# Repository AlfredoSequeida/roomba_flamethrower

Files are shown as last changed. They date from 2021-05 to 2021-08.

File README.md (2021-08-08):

# Roomba Flamethrower
[Watch the video here](https://youtu.be/nNa-5zJv5F0)

demo

This repo contains all of the code, schematics, and 3d models for the Roomba Flamethrower project.

## Setup
This project uses a Raspberry pi Zero W running [Raspberry Pi OS Lite](https://www.raspberrypi.org/software/operating-systems/) as the "brains" of the build. Python 3.5 or newer is required to run the software.

- To use hardware-timed servo pulses and thus avoid jittering from multiple servos being controlled by the pi, this project uses the pigpio library. 
- The Xbox one controller is handled using evdev.
- Serial communication between the Roomba and the raspberry pi is handled using pyserial.

To facilitate the setup process, this repo includes a setup script. To run it, simply run the following command from the project's root directory

```
sudo sh setup.sh
```

In addition, if you want to set up the program to run on boot for a better user experience. You can use `crontab` to set up a cronjob for the intended user. As an example for the default `pi` user.

```
crontab -u pi -e
```

Then run the script on boot by adding the following line to the file.

```
@reboot python3 /full/path/to/project/dir/roomba_flamethrower/roomba_flamethrower/main.py
```

Then save the file. A quick note of caution, the Roomba class initiates a serial connection with the Roomba using `safe` mode by default. However, if you decide to change the mode to something else, you need to add the logic to properly return the Roomba to `safe` mode to avoid battery drain.

As part of the setup, you also need to pair the Xbox One Controller and the raspberry pi.

Disable Enhanced Re-Transmission Mode (not supported by the Xbox One Controller)
```
echo 'options bluetooth disable_ertm=Y' | sudo tee -a /etc/modprobe.d/bluetooth.conf
```

start bluetoothctl 
```
sudo bluetoothctl
```

Start pairing mode on the Xbox One controller and scan for the controller
```
agent on
default-agent
scan on
```

once you see the controller appear, connect to it using its address
```
connect XX:XX:XX:XX:XX:XX
```

trust the controller using its address for automatic connections on boot
```
trust XX:XX:XX:XX:XX:XX
```

### Controlls
By default, these are the control mappings for the Xbox One controller.

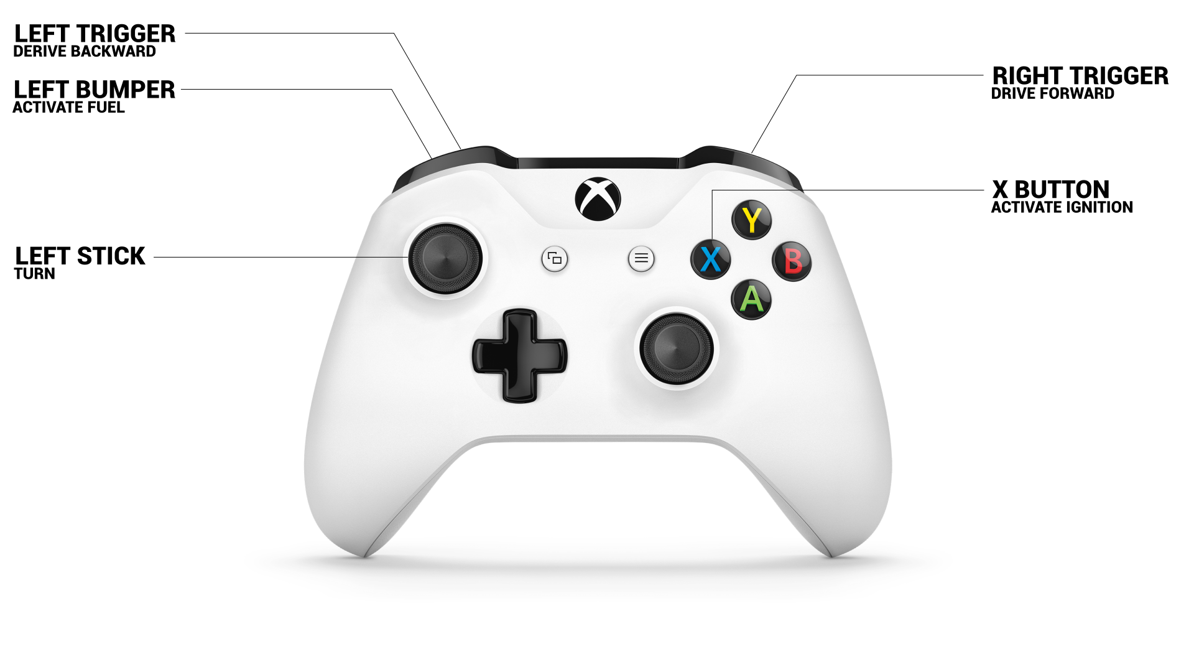
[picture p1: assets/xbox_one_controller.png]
controll mappings


If you want to change them, you can change the conditional statements in `main.py` in the `main()` function, which are found inside the for loop.

## Build
To build this project, the following parts were used:
- [(1) Raspberry Pi Zero W](https://www.raspberrypi.org/products/raspberry-pi-zero-w/)
- [(1) Micro USB Male to USB Female OTG Adapter](https://www.amazon.com/Ksmile®-Female-Adapter-SamSung-tablets/dp/B01C6032G0)
- (1) Xbox One Bluetooth Controller (1708)
- (1) Irobot Roomba 770
- [(1) Irbot Communication Cable for Create® 2](https://store.irobot.com/default/parts-and-accessories/create-accessories/communication-cable-for-create-2/4466502.html)
- [(2) 35kg-cm servos](https://www.amazon.com/ZOSKAY-Coreless-Digital-Stainless-arduino/dp/B07S9XZYN2)
- [(1) 12kg-cm servo](https://www.amazon.com/4-Pack-MG996R-Torque-Digital-Helicopter/dp/B07MFK266B)
- [(1) M2.5 brass stanoff kit](https://www.amazon.com/LBY-Multi-function-Combination-Screwdriver-Green/dp/B07GK6812D)
- [Neon 7X Refined Butane Gas Pack](https://www.amazon.com/Neon-Refined-Butane-300ml-Pack/dp/B072FR3LT2)
- [(1) Arc Lighter](https://www.amazon.com/lcfun-Waterproof-Windproof-Rechargeable-Flameless-Plasma-Camouflage/dp/B07GCHLDWR)
- [(1) USB Solar Power Bank](https://www.amazon.com/gp/product/B07T2NRK8G)
- [(1) USB A Male to Micro USB cable](https://www.amazon.com/10ft3Pack-Charging-Smartphone-Connection-Blackwhite/dp/B06XYH75NQ)

If you don't have it already, you may also need wire, solder, and a soldering iron.

In addition, to use the included 3d models, you will also need a 3d printer. I used the [Creality Ender 3 V2](https://www.amazon.com/Creality-Printer-Printing-Function-220x220x250mm/dp/B07FFTHMMN) and [White eSUN PLA+](https://www.amazon.com/eSUN-1-75mm-Printer-Filament-2-2lbs/dp/B01EKEMFQS) filament.

### 3D printing
All of the parts were printed using 10% infill with a 0.28mm layer height. The bed was set to 60° Celcius and the extruder to 225° Celcius. With the exception of the Raspberry Pi Zero base, all of the models were printed without using supports.

### Assembly
Besides the Roomba part of the build, the flame thrower part of the build is centered around the butane bottle.

The [bottle stand](https://github.com/AlfredoSequeida/roomba_flamethrower/blob/main/models/bottle_stand.stl) can be used to attach the butane bottle to the Roomba using an adhesive. An option like Hot Glue can allow you to easily remove it later by heating the glue back up.

Attached to the bottle stand you cand you can use string or rope along with the provided [hooks](https://github.com/AlfredoSequeida/roomba_flamethrower/blob/main/models/hook.stl) to latter hold down the bottle adapter when the butane servo uses a downward force to spray the bottle. 

The [bottle adapter](https://github.com/AlfredoSequeida/roomba_flamethrower/blob/main/models/bottle_adapter.stl) holds the two 35kg servos using the provided hardware, The butane servo uses the smaller plastic propeller with an M2.5 standoff through one of the holes, which aids in pressing down the [cap of the butane bottle](https://github.com/AlfredoSequeida/roomba_flamethrower/blob/main/models/cap.stl) and the lighter assembly servo uses the larger plastic propeller with two screws for holding down the servos attached to the [lighter assembly](https://github.com/AlfredoSequeida/roomba_flamethrower/blob/main/models/lighter_assembly.stl).

bottle adapter

Attached to the back portion of the bottle adapter is the [Raspberry Pi Zero base](https://github.com/AlfredoSequeida/roomba_flamethrower/blob/main/models/rpi_zero_base.stl). This base is set up with four M2.5 standoffs using screws on the underside. This is why the base has larger 4mm cylindrical cutouts on the underside. This provides a flush base that can be glued to the bottle adapter.

raspberry pi base

The lighter assembly holds the 12kg servo and the arc lighter. The servo is held in place and lifted using 3 brass standoffs. In addition, to press the button on the arc lighter, the metal adapter from the 35kg servos is attached. This is because this adapter has a much larger surface area compared to the included plastic adapters.

lighter assembly

## Wiring
To wire everything together, refer to the following schematic:

schematic

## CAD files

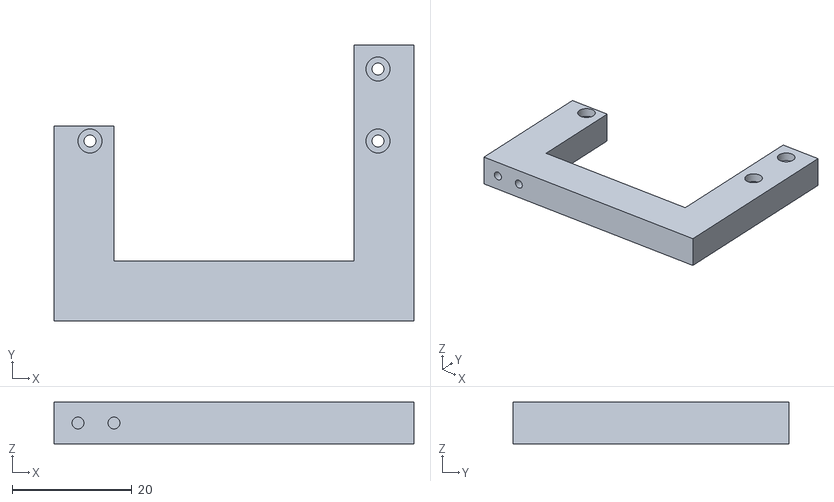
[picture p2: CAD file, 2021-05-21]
models/lighter_assembly.stl
60.0 x 46.0 x 7.00

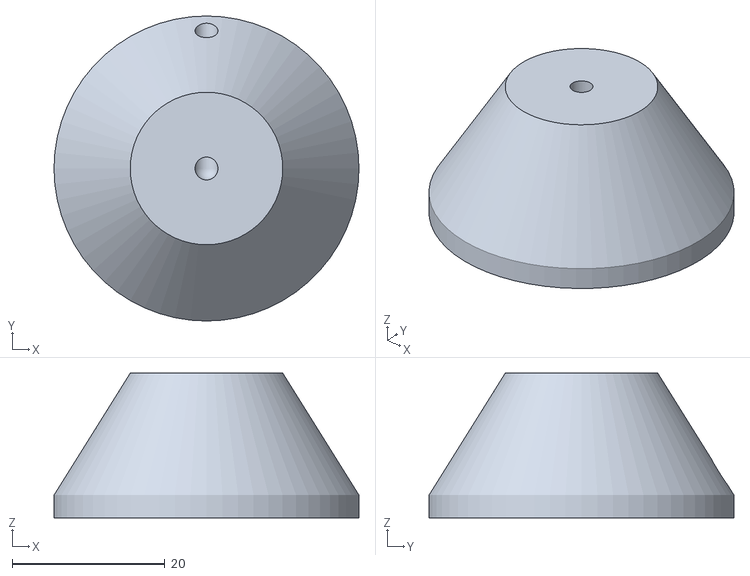
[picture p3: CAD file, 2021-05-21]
models/cap.stl
40.0 x 40.0 x 19.0

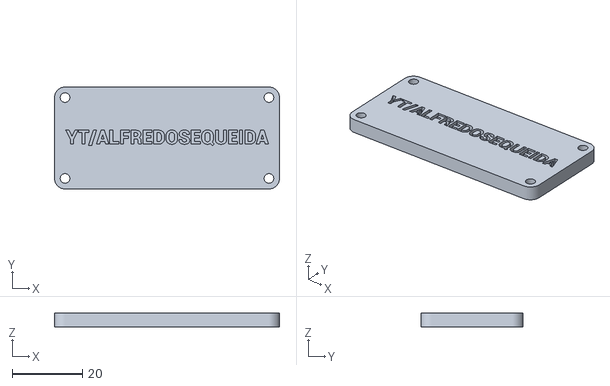
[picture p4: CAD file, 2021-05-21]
models/rpi_zero_base.stl
64.0 x 29.0 x 4.00

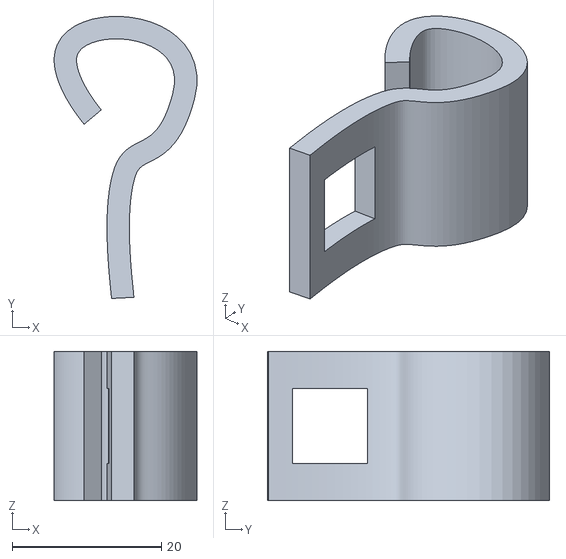
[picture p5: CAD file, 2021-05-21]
models/hook.stl
19.1 x 37.8 x 20.0

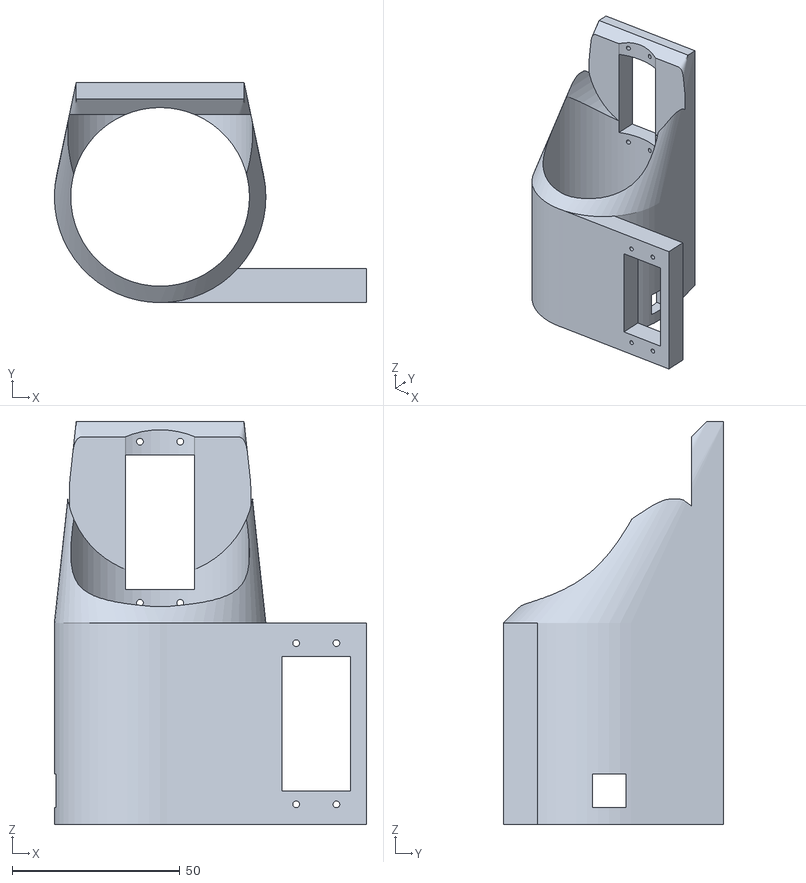
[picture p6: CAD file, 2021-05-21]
models/bottle_adapter.stl
93.0 x 65.6 x 120.0

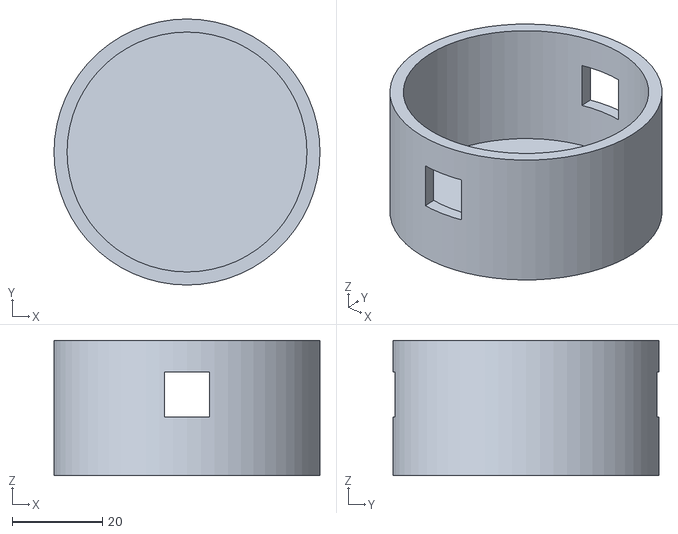
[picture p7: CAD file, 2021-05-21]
models/bottle_stand.stl
59.0 x 59.0 x 30.0

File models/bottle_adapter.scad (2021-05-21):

$fn=60;
bottle_r = 53/2;

holder_thickness = 5;

servo_y = 12;
servo_x = 20;
servo_z = 40;


// servo insert test
//difference(){
//    
//    bottle_adapter();
//
//    translate([15,-50,0])
//    cube([50,100,100]);
//
//    translate([-80,-50,0])
//    cube([100,50,100]);
//
//    translate([-65,-50,0])
//    cube([50,100,100]);
//}

bottle_adapter();

module bottle_adapter(){
    adapter_h = 120;
    insert_padding = 0.1;
    butane_channel_r = 10;
    butane_channel_h = 20;
    
    flat_surface_width = 50;
    
    servo_rotor_depth = 20;
    cap_depth = 8;
    
    servo_cutout_r = 56/2;
    
    hook_insert = 10;
    
    lighter_assembly_servo = [servo_x+40, servo_y-2, servo_z+20];

    difference(){
        union(){
        hull(){
            // butane servo
            translate([0,
                       bottle_r + holder_thickness + insert_padding,
                       adapter_h/2
                     ])
            rotate([0,0,90])
            cube([holder_thickness,
                  flat_surface_width,
                  adapter_h],
                center=true);

            cylinder(r=bottle_r + holder_thickness, h=adapter_h/2);
        }
            translate([bottle_r -25,
               -bottle_r/3 - servo_y *1.88,
               0
             ]){
        difference(){
            cube(lighter_assembly_servo);
    
            translate([(lighter_assembly_servo[0])/2 + 15,
                        lighter_assembly_servo[1]/1.3,
                        lighter_assembly_servo[2]/6])
            servo_insert();
        }
    }
    }
        
        cylinder(r=bottle_r + insert_padding, h=200);
        
        // servo insert
        translate([0,
                   bottle_r + holder_thickness,
                   adapter_h - servo_z - 10
                 ])
        servo_insert();
        
        translate([0,
                   bottle_r-2,
                   adapter_h - servo_cutout_r+10])
        rotate([90,0,0])
        cylinder(r=servo_cutout_r, h=20);
        
        translate([0,0,hook_insert])
        cube([100, hook_insert,hook_insert],center=true);
    }
}

module servo_insert(){
    offset = 7;
    
    screw_r = 2/2;
    normal_screw_r = 4/2;
    z_offset = 2;
    
    insert_padding = 0.5;
    insert_thickess = 20;
    
    holder_spacing_from_center = 4 + normal_screw_r;
    
    translate([0,0,servo_z/2])
    cube([insert_thickess + insert_padding,
          insert_thickess + insert_padding,
          servo_z],center=true);
    
    // top holes
    color("gold")
    translate([-holder_spacing_from_center,
               0,
               servo_z + z_offset + normal_screw_r
             ])
    rotate([90,0,0])
    cylinder(r=screw_r, h=insert_thickess, center=true);
    
    color("red")
    translate([-holder_spacing_from_center,
               insert_thickess/4,
               servo_z + z_offset + normal_screw_r
             ])
    rotate([90,0,0])
    cylinder(r=normal_screw_r, h=insert_thickess/2, center=true);
    
    color("gold")
    translate([holder_spacing_from_center,
               0,
               servo_z + z_offset + normal_screw_r
             ])
    rotate([90,0,0])
    cylinder(r=screw_r, h=insert_thickess, center=true);
    
    color("red")
    translate([holder_spacing_from_center,
               insert_thickess/4,
               servo_z + z_offset + normal_screw_r
             ])
    rotate([90,0,0])
    cylinder(r=normal_screw_r, h=insert_thickess/2, center=true);
    
    // bottom holes
    color("gold")
    translate([-holder_spacing_from_center,
               0,
               -z_offset - normal_screw_r
             ])
    rotate([90,0,0])
    cylinder(r=screw_r, h=insert_thickess, center=true);
    
    color("red")
    translate([-holder_spacing_from_center,
               insert_thickess/4,
               -z_offset - normal_screw_r
             ])
    rotate([90,0,0])
    cylinder(r=normal_screw_r, h=insert_thickess/2, center=true);
    
    color("gold")
    translate([holder_spacing_from_center,
               0,
               -z_offset - normal_screw_r
             ])
    rotate([90,0,0])
    cylinder(r=screw_r, h=insert_thickess, center=true);
    
    color("red")
    translate([holder_spacing_from_center,
               insert_thickess/4,
               -z_offset - normal_screw_r
             ])
    rotate([90,0,0])
    cylinder(r=normal_screw_r, h=insert_thickess/2, center=true);
}

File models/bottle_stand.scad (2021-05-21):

$fn=60;
bottle_r = 53/2;
insert_padding = 0.1;

stand_h = 30;
thickness = 3;

difference(){
    cylinder(r=bottle_r + thickness,h=stand_h);
    translate([0,0,thickness])
    cylinder(r=bottle_r + insert_padding,h=stand_h);
    
    translate([0,0,thickness + stand_h/2])
    cube([10,100,10],center=true);
}

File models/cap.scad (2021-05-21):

$fn=60;

x = 3;
y = 3;
z = 8;
r = 10;

top_z = 16;
top_r = 40/2;

translate([0,0,top_z + y])
rotate([180,0,0])
cap();

module cap(){
    difference(){
        hull(){
            translate([0,0,top_z])
            cylinder(r=top_r, 3);
            cylinder(r=r,h=z);
        }
        nozzle();
    }
}

module nozzle(){
    insert_h = 13;
    nozzle_r = 2.8/2;

    insert_padding = 0.1;
    prism_s = nozzle_r*2;

    union(){
        cylinder(r=nozzle_r + insert_padding,h=insert_h);

        translate([0,0,insert_h])
        sphere(r=nozzle_r + insert_padding);
        
        translate([0,0,insert_h])
        rotate([90,0,0])
        cylinder(r=nozzle_r + insert_padding,h=insert_h + 10);
    }
}

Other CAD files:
models/hook.scad
models/lighter_assembly.scad
models/rpi_zero_base.scad

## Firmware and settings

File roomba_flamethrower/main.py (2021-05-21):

from Controller import Controller
from FlameThrower import FlameThrower
from Roomba import Roomba

from time import sleep


def get_controller(roomba) -> Controller:
    """Wait for controller to connect and return a Controller instance once the
    controller has been connected
    """

    controller = None

    while not controller:
        try:
            controller = Controller()
            roomba.play_ready_sound()
            print("ready")
        except:
            print("Waiting for controller . . .")
            roomba.play_waiting_sound()
            sleep(3)

    return controller


def get_trig_val(abs_val: int, max_unit: int, abs_limit: int) -> int:
    """Get the corresponding trigger value to a specific limit. This evenly
    devides the value so that the more you press the trigger, the higher the
    output value.

    abs_val - The current trigger value
    max_unit - The maximum value to remap the trigger value
    abs_limit - The maximum range of the trigger
    """

    inc = abs_limit / max_unit
    return int(abs_val / inc)


def get_unsigned_js_val(abs_val: int, max_unit: int, abs_limit: int) -> int:
    """Get unsigned remaped joystick value in reverse range
    (For example if the limit is 2000, and the input valueis also 2000,
    the value returned will be 1. And with the same limit, if the input value
    is 1, the output value wwill be 2000. The same applies to the values in
    between). This evenly devides the value so that the maximum js range is
    remapped to a value in the range of the
    specified limit.

    abs_val - The current joystick value
    max_unit - The maximum value to remap the joystick value
    abs_limit - The maximum range of the joystick
    """

    inc = abs_limit / max_unit

    # ignoring signs to keep results positive
    if abs_val > 0:
        abs_val *= -1

    val = int((abs_val / inc) + max_unit)

    # if the value is zero, return 1 (maximum range)
    if val == 0:
        val = 1

    return val


def main():

    fuel_pin = 17
    ignition_pin = 27
    assembly_pin = 22

    roomba_serial = "/dev/ttyUSB0"

    with Roomba(roomba_serial) as roomba, FlameThrower(
        fuel_pin, ignition_pin, assembly_pin
    ) as flame_thrower:
        controller = get_controller(roomba)

        # turning radius in mm
        rad = 0
        # driving direction, negative = backwards, positive = forwards
        rot = 0
        # driving velocity in mm/s
        vel = 0

        for button, val in controller.get_input():

            update = False

            # use right trigger to drive forward
            if button == "RT":
                vel = get_trig_val(val, Roomba.MAX_VEL, controller.TRIG_MAX_RANGE)
                rot = 1
                update = True

            # use left trigger to drive backward (reverse)
            if button == "LT":
                vel = get_trig_val(val, Roomba.MAX_VEL, controller.TRIG_MAX_RANGE)
                rot = -1
                update = True

            # use the left joystick to turn
            if button == "LSX":
                rad = get_unsigned_js_val(val, Roomba.MAX_RAD, controller.JS_CENTER)

                if val > 0:
                    rad *= -1

                update = True

            # send new command to romba
            if update:
                roomba.drive(vel * rot, rad)

            # use left bumper to spray fuel.
            # Pressed = spay, Stop pressing = stop spraying
            if button == "LB":
                if val == 1:
                    flame_thrower.fuel_on()
                else:
                    flame_thrower.fuel_off()

            # use x button to move ignition source in the fuel's path and
            # turn on the ignition source.
            # Press to enable, let go to disable
            if button == "X":
                if val == 1:
                    flame_thrower.assembly_on()
                    flame_thrower.ignition_on()
                else:
                    flame_thrower.assembly_off()
                    flame_thrower.ignition_off()


if __name__ == "__main__":
    main()

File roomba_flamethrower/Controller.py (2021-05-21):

from evdev import InputDevice, list_devices, ecodes


class Controller:

    # xbox one controller joystick max range (negative + positive range)
    JS_MAX_RANGE = 65534

    # xbox one controller joystick center range 
    JS_CENTER = JS_MAX_RANGE / 2

    # xbox one controller trigger max range (pressed in all of the way)
    TRIG_MAX_RANGE = 1023

    # button mappings for xbox one controller
    BUTTONS = {
        0: "LSX",
        1: "LSY",
        2: "RSV",
        4: "SCAN",
        5: "RSH",
        9: "RT",
        10: "LT",
        16: "DPADHOR",
        17: "DPADVERT",
        158: "OPTION",
        172: "HOME",
        304: "A",
        305: "B",
        308: "Y",
        307: "X",
        310: "LB",
        311: "UNK",
        315: "START",
        317: "LSB",
        318: "RSB",
    }

    def __init__(self):
        self.controller = InputDevice(list_devices()[0])

    def get_input(self) -> list:
        """
        Get contoller input from linux input devices.
        """
        for e in self.controller.read_loop():

            key_code = e.code
            button = self.BUTTONS[key_code]

            if e.type == ecodes.EV_KEY:
                val = e.value
                yield (button, val)

            # for abs values (joystick, triggers)
            if e.type == ecodes.EV_ABS:
                val = e.value
                button = self.BUTTONS[key_code]

                # getting left joystick x-axis values (used for turning)
                if button == "LSX":
                    # Splitting maximum joystick range into postive and negative
                    # values. Negative = left, Positive = right
                    val = val - self.JS_CENTER

                yield (button, val)

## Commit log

2021-05-21 updated schematic
2021-05-21 updated cap model
    [cap.scad, cap.stl]
